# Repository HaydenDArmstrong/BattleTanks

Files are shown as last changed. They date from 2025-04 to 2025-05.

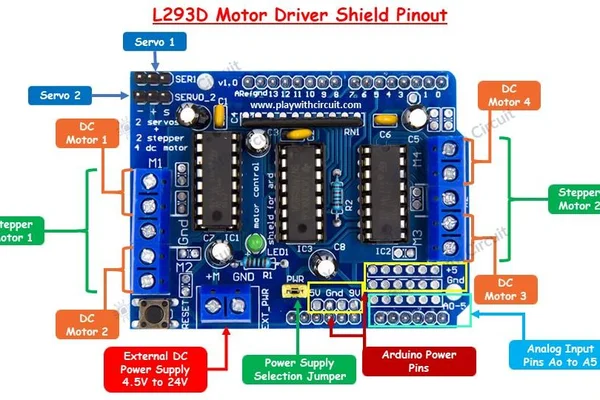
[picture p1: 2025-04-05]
Diagrams/l293d pinout.png

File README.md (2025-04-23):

# LaserTanks

## Battle Tank Fizz File
made a diagram in Fritzing to show how Battle tank wires.

## ControllerOutputToArduino
- Code to be uploaded to the **ESP32**.
- The ESP32 connects to the **controller** and outputs controller information, including:
  - Button press state
  - D-pad press state
  - Thumbstick axis data
- This is accomplished mainly through the **BluePad32** library.
- Data is sent to the **Arduino** through the transmission pin out and recieving pin in.

## ArduinoSide
- Code to be uploaded to the **Arduino**.
- The tank uses an **L293D motor** to power the **motors, laser emitter, and laser receiver**.
- This code includes:
  - Reading ESP32 controller information and acting on it (button functions, thumbstick mapping).
  - Initialization function to validate basic tank functionality.
  - Future game functionality development.

- The **PWMServo** library is used instead of the normal **Servo** library to prevent jitter when both the **servo and ESP32** are active. This issue arises due to **SoftwareSerial**, which uses interrupts whenever a character is sent, affecting servo motion.

- The **L293D motor shield** is mounted on the board and serves as the base for GPIO connections. The corresponding pin connections are as follows:

## Servo Pins
- **SERVO1** – Up/Down turret servo motor  
- **SERVO2** – Left/Right turret servo motor  

## DC Motor Wiring (Tread Movement)
- **Left Motor** → Connect to **M1**  
- **Right Motor** → Connect to **M2**  

### Left Motor (Nearest to USB Port)
- **Black (GND)** → First pin (ground)  
- **Red (PWR)** → Second pin (power)  
- **Middle GND slot** remains empty  

### Right Motor
- **Black (GND)** → Leftmost pin (next to middle GND)  
- **Red (PWR)** → Rightmost pin  

## Misc Wiring (Analog Pins)
- **A0**: *Laser Receiver*  
- **A1**: *Laser Receiver*  
- **A2**: *(Unused)*  
- **A3**: Laser emitter pin  
- **A4**: ESP32 Receiving IN (connect to ESP32 pin **17**)  
- **A5**: ESP32 Transmit OUT (connect to ESP32 pin **16**)  

## ESP32 Notes
- **ESP32 Pin 17** → **TX (Transmits)**  
- **ESP32 Pin 16** → **RX (Receives)**  
- **TX of ESP32 must connect to RX of the board and vice versa.**

### Power Requirements
- **ESP32 requires a separate and adequate power source** to avoid voltage issues.
- MAKE SURE THE LASER RECIEVER HAS THE PHOTORESISTOR IN THE RIGHT DIRECTION (NUB FACING TOWARDS PINS) OR SHIT GONNA BURN.

### Grounding
- **ESP32 must share a common ground with the board. Make sure to properly ground all the components.**

## TODO
- **Correct Servo Movement:** Ensure smooth and delay-free movement of the tank servos from controller input. *(The tank servos are controlled via the right thumbstick.)*
- **Remove Archaic Functions and Code:** Delete unused code, such as KB and BT functions, prototyping code, etc.
- **Develop an Advanced Laser Game:** The current laser game is basic and lacks necessary features.
- **Add a Life Screen:** Display remaining lives before the game ends. This is challenging due to the limited pinout of the **ESP32** and **motor shield**. However, with one extra pin available (if only two laser receivers are used), a small digital screen might be implemented using a single signal pin.

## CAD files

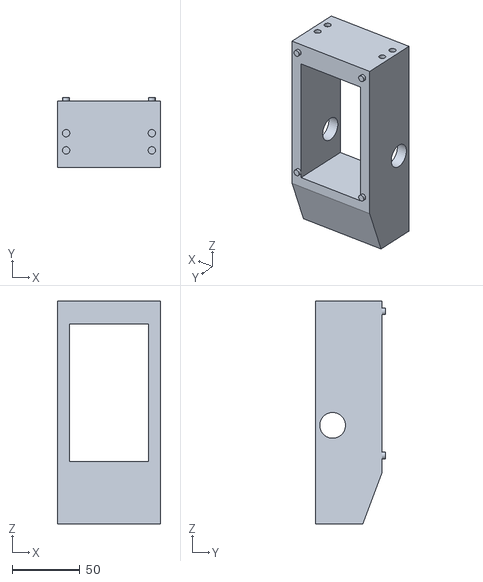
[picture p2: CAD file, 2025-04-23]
3D_Parts/Front Body.STL
76.2 x 51.8 x 165.1

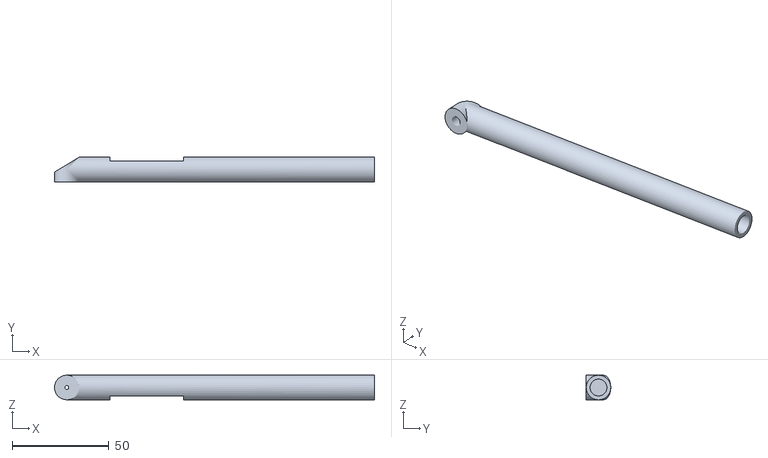
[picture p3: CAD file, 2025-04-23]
3D_Parts/Barrel.STL
165.1 x 12.7 x 12.7

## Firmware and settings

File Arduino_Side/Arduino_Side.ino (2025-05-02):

#include <PWMServo.h>
#include <SoftwareSerial.h>

// ESP32 Controller communication
SoftwareSerial espSerial(A4, A5); // RX, TX
String espData = "";
bool newEspData = false;

// Initialized function: Makes sure all parts work as they should
bool hasInitialized = false;

// Player "Lives". Always starts at 5. If you want to change the number of lives, change startingLives
const int startingLives = 5;
int lives = startingLives;

// Servo globals
PWMServo LRServo;
const int LRServoPin = 10; // Pin for "Servo 1" on l293d

PWMServo UDServo;
const int UDServoPin = 9; // Pin for "Servo 1" on l293d

// Laser receiver globals
const int laserReceiverLeftPin = A2;
const int laserReceiverRightPin = A1;
const int laserReceiverMiddlePin = A0;
const int laserTurret = A3;

// Motor sensor globals
const int PWML = 11;      // M1 motor left side pwm2a
const int PWMR = 5;       // M2 motor right side pwm0b
const int DIR_CLK = 4;    // Data input clock line
const int DIR_EN = 7;     // Enable pins
const int DATA = 8;       // USB cable
const int DIR_LATCH = 12; // Output memory latch clock



// Directional constants
const int aFwd = 39;      // Move Forward
const int aBwd = 216;     // Move Backward
const int CW = 116;       // Left translation (L moves up, R moves down)
const int CCW = 139;      // Right translation (L moves down, R moves up)
const int Stop = 0;       // Parking variable
const int LeftFwd = 36;   // Upper Left Move
const int RightFwd = 3;   // Upper Right Move
const int RightBwd = 80;  // Lower Left Move (right backward)
const int LeftBwd = 136;  // Lower Right Move

// extra movement options: obsolete due to two motor design.
// const int Right_Rotate = 149;      // Rotate Right
// const int Left_Rotate = 106;       // Rotate Left
// const int Drift_Left = 20;         // Drift on Left
// const int Drift_Right = 10;        // Drift on Right

// Set the default speed between 1 and 255
int SpeedL = 150;
int SpeedR = 150;

void setup() {
  // Serial communication
  Serial.begin(9600);
  espSerial.begin(9600);

  // Attach servo to pin
  LRServo.attach(LRServoPin);
  UDServo.attach(UDServoPin);

  // Define laser receiver and emitters
  pinMode(laserReceiverLeftPin, INPUT);
  pinMode(laserReceiverRightPin, INPUT);
  pinMode(laserTurret, OUTPUT);

  // Define motor pins
  pinMode(DIR_CLK, OUTPUT);
  pinMode(DATA, OUTPUT);
  pinMode(DIR_EN, OUTPUT);
  pinMode(DIR_LATCH, OUTPUT);
  pinMode(PWMR, OUTPUT);
  pinMode(PWML, OUTPUT);

  // Initial debug
  Serial.println("Setup complete. Starting loop...");                               

}

void loop() {
  if (lives > 0) {

       if (!hasInitialized) {
         initial();  // Call the initial setup function
       }

    // Check for new controller data
    readEspControllerData();

    // Process controller data if new data is available
    processControllerData();

  } else if (lives == 0) {
    Serial.println("No lives left. Game Over!");
    digitalWrite(laserTurret, LOW);
    Motor(Stop, 0, 0);
    lives = -1;

  } else {
    // Effectively stop Arduino and loop. Except an if statement where if '5' is put in serial terminal, the lives refill
    if (Serial.available() > 0) {
      int command = Serial.parseInt(); // Read the command from Serial
      if (command == 5) {
        lives = startingLives; // Refill lives to 5
        Serial.println("Lives refilled to 5!");
      }
    }
  }
}

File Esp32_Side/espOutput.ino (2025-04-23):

#include <Bluepad32.h>
#include <HardwareSerial.h>


HardwareSerial SerialPort(2); // Use hardware serial port 2

ControllerPtr myControllers[BP32_MAX_GAMEPADS];

// This callback gets called any time a new gamepad is connected.
void onConnectedController(ControllerPtr ctl) {
  bool foundEmptySlot = false;
  for (int i = 0; i < BP32_MAX_GAMEPADS; i++) {
    if (myControllers[i] == nullptr) {
      Serial.printf("CALLBACK: Controller is connected, index=%d\n", i);
      ControllerProperties properties = ctl->getProperties();
      Serial.printf("Controller model: %s, VID=0x%04x, PID=0x%04x\n", ctl->getModelName().c_str(), properties.vendor_id, properties.product_id);
      
      // Send controller connection message to Arduino
      SerialPort.println("Controller connected!");
      
      myControllers[i] = ctl;
      foundEmptySlot = true;
      break;
    }
  }

  if (!foundEmptySlot) {
    Serial.println("CALLBACK: Controller connected, but could not found empty slot");
  }
}

void onDisconnectedController(ControllerPtr ctl) {
  bool foundController = false;

  for (int i = 0; i < BP32_MAX_GAMEPADS; i++) {
    if (myControllers[i] == ctl) {
      Serial.printf("CALLBACK: Controller disconnected from index=%d\n", i);
      
      // Send controller disconnection message to Arduino
      SerialPort.println("Controller disconnected!");
      
      myControllers[i] = nullptr;
      foundController = true;
      break;
    }
  }

  if (!foundController) {
    Serial.println("CALLBACK: Controller disconnected, but not found in myControllers");
  }
}

// Process gamepad and send button states to Arduino
void processGamepad(ControllerPtr ctl) {
  // Store the previous button state to detect changes
  static uint16_t prevButtons = 0;
  static uint8_t prevDpad = 0;
  static int16_t prevAxisX = 0;
  static int16_t prevAxisY = 0;
  static int16_t prevAxisRX = 0;
  static int16_t prevAxisRY = 0;
  
  // Check if any state (including right stick) has changed
    // if (ctl->buttons() != prevButtons || ctl->dpad() != prevDpad || 
    //     abs(ctl->axisX() - prevAxisX) > 25 || abs(ctl->axisY() - prevAxisY) > 25 ||
    //     abs(ctl->axisRX() - prevAxisRX) > 25 || abs(ctl->axisRY() - prevAxisRY) > 25) {
    
    // Send button state and stick positions to Arduino
    SerialPort.print("BTN:");
    SerialPort.print(ctl->buttons(), HEX);
    SerialPort.print(",DPAD:");
    SerialPort.print(ctl->dpad(), HEX);
    SerialPort.print(",LX:");
    SerialPort.print(ctl->axisX());
    SerialPort.print(",LY:");
    SerialPort.print(ctl->axisY());
    SerialPort.print(",RX:");
    SerialPort.print(ctl->axisRX());
    SerialPort.print(",RY:");
    SerialPort.println(ctl->axisRY());
    
    // Also print to local serial for debugging
    Serial.print("Sent to Arduino - BTN:");
    Serial.print(ctl->buttons(), HEX);
    Serial.print(",DPAD:");
    Serial.print(ctl->dpad(), HEX);
    Serial.print(",LX:");
    Serial.print(ctl->axisX());
    Serial.print(",LY:");
    Serial.print(ctl->axisY());
    Serial.print(",RX:");
    Serial.print(ctl->axisRX());
    Serial.print(",RY:");
    Serial.println(ctl->axisRY());
    
    // Update previous states
    prevButtons = ctl->buttons();
    prevDpad = ctl->dpad();
    prevAxisX = ctl->axisX();
    prevAxisY = ctl->axisY();
    prevAxisRX = ctl->axisRX();
    prevAxisRY = ctl->axisRY();
    // }

  // Example of detecting button presses (for reference)
  // PS4 X button (0x0001)
  if ((ctl->buttons() & 0x0001) && !(prevButtons & 0x0001)) {
    SerialPort.println("X button pressed");
  }
  
  // PS4 Circle button (0x0002)
  if ((ctl->buttons() & 0x0002) && !(prevButtons & 0x0002)) {
    SerialPort.println("Circle button pressed");
  }
  
  // PS4 Square button (0x0004)
  if ((ctl->buttons() & 0x0004) && !(prevButtons & 0x0004)) {
    SerialPort.println("Square button pressed");
  }
  
  // PS4 Triangle button (0x0008)
  if ((ctl->buttons() & 0x0008) && !(prevButtons & 0x0008)) {
    SerialPort.println("Triangle button pressed");
  }
}


void processControllers() {
  for (auto myController : myControllers) {
    if (myController && myController->isConnected() && myController->hasData()) {
      if (myController->isGamepad()) {
         processGamepad(myController);
      }
      else {
        Serial.println("Unsupported controller");
      }
    }
  }
}

// Arduino setup function
void setup() {
  // Initialize Serial Monitor for debugging
  Serial.begin(115200);
  Serial.printf("Firmware: %s\n", BP32.firmwareVersion());
  
  // Initialize Serial2 for Arduino communication with RX on GPIO 16, TX on GPIO 17
  SerialPort.begin(9600, SERIAL_8N1, 16, 17);
  Serial.println("ESP32 Controller to Arduino communication initialized");
  
  const uint8_t* addr = BP32.localBdAddress();
  Serial.printf("BD Addr: %2X:%2X:%2X:%2X:%2X:%2X\n", addr[0], addr[1], addr[2], addr[3], addr[4], addr[5]);

  // Setup the Bluepad32 callbacks
  BP32.setup(&onConnectedController, &onDisconnectedController);
  BP32.forgetBluetoothKeys();
  BP32.enableVirtualDevice(false);
  
  // Send initial message to Arduino
  SerialPort.println("ESP32 controller system ready!");
}
unsigned long lastSendTime = 0;
const unsigned long sendInterval = 10; // send every 50ms

void loop() {
 
   // This call fetches all the controllers' data
  bool dataUpdated = BP32.update();
  if (dataUpdated )
    processControllers();

  delay(2); // Shorter delay for more responsive controls
}

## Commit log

2025-04-05 Update and rename proto_ArduinoSide.ino to ArduinoSide.ino
2025-04-23 Organize Files
    [Barrel.STL, BattleTank.fzz, Front Body.STL]
2025-05-02 Update Esp32_side
